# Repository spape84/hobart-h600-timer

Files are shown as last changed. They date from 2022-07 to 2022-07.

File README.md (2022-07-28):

# hobart-h600-timer
A timer pcb including 3D-printed parts and code for Hobart H600 mixing machines

## What is this about?
This repository contains everything you need to retrofit a Hobart H600 mixing machine with a timer and to build a new operating panel for the machine. I bought a Hobart H 600 (3-phase)/380V from a bakery, which went bankrupt and refurbished the machine. As the whole machine was dirty especially the operating panels I chose to replace them and add a timer function to the machine. Everything I have done is included here.

## Pictures before
tbd

## Pictures after
tbd

## Operating panel
I chose to redesign the operating panel to make it compliant to current standards. So I needed a switch to turn the machine on, another to turn it off, an emergency button, a rotary dial knob for the timer, as well as a 7-digit display.

The operating panel is only 159mm x 83mm, which is not much space for the elements planned.

You could use the file for the operating panel "Panel-0069.dxf" for laser cutting an aluminium or stainless-steel panel. I chose stainless-steel. On top of the panel I put an emergency-off button Eaton M22-PV/K11, below is a combined on/off button with control LED Eaton M22-DDL-GR-X0/X1/-A/-LED-W/-K10/-K01. The bottom row is divided into space for the 7-segment display (Adafruit 0.56" 4-Digit 7-Segment Display w/I2C Backpack) and a rotary encoder button Alps STEC12E07.

I am currently designing a backplane for the stainless-steel panel to hold the 7-segment display and the rotary encoder. So this is not ready, yet.

## Bill of materials

This is an almost complete table of everything I needed to build the new operating panel and the timer retrofit.

|Element |Producer |Product-No. |Webshop |
|---|---|---|---|
|Operating panel |self/CNC |Panel-0069.dxf |https://mipart.com/ |
|Backplane |self/3D-Print |Backplane.stl |https://mipart.com/ |
|7-segment display |Adafruit |0.56" 4-Digit 7-Segment Display |https://www.reichelt.de/ |
|Rotary Encoder |Alps |STEC12E07 |https://www.reichelt.de/ |
|PCB |self/PCB |Hobart H600 Timer.fzz |https://aisler.net/p/ZWIEMOXD|
|0603 1kohm Resistor |any |SMD-0603 1,0K |https://www.reichelt.de/ |
|0603 10kohm Resistor |any |SMD-0603 10K |https://www.reichelt.de/ |
|Transistor, SOT-23 |NXP |BC 817-40 |https://www.reichelt.de/ |
|Diode TS 4148 |any |TS 4148 |https://www.reichelt.de/ |
|Relay |Weidmueller |RCI 314012 |https://www.reichelt.de/ |
|Switching PSU |Meanwell |IRM-03-12 |https://www.reichelt.de/ |
|Arduino Nano every |Arduino |ABX00028 |https://www.reichelt.de/ |
|Terminal connector (2x) |WAGO |236-403 |https://www.reichelt.de/ |
|Terminal block |Camdenboss |CTB0502-2 |https://www.reichelt.de/ |
|Molex connector |Molex |26604040 |https://www.reichelt.de/ |
|Header w/ 2 pins 2.54 |any | |https://www.reichelt.de/ |
|Header w/ 3 pins 2.54 |any | |https://www.reichelt.de/ |
|Emergency off button |Eaton |216516 - M22-PV/K11 |https://www.automation24.de/ |
|Double pushbutton |Eaton |216700 - M22-DDL-GR-X1/X0 |https://www.automation24.de/ |
|LED element |Eaton |216557 - M22-LED-W |https://www.automation24.de/ |
|Contact element |Eaton |216378 - M22-K01 |https://www.automation24.de/ |
|Contact element |Eaton |216376 - M22-K10 |https://www.automation24.de/ |
|Mounting adapter |Eaton |216374 - M22-A |https://www.automation24.de/ |
|PCB Carrier |self/3D-Print |Timer-Mainboard-Carrier.stl |https://mipart.com/ |

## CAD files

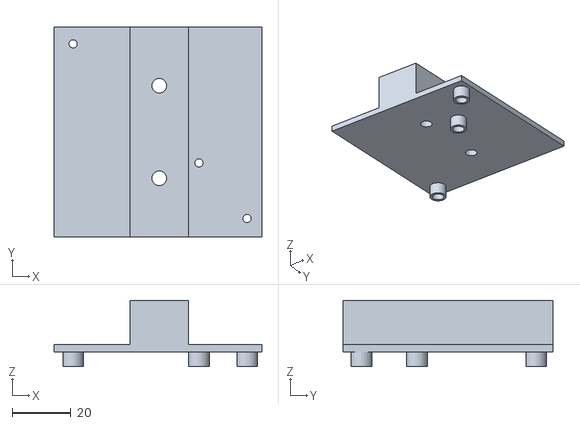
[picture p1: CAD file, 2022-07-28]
3D Print/Timer-Mainboard-Carrier.stl
70.6 x 71.4 x 22.5

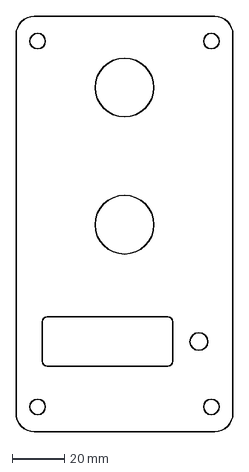
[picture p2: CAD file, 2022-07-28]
Panel/Panel-0069.dxf
83.0 x 159.0 mm

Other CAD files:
3D Print/Timer-Mainboard-Carrier_tweaked.stl
3D Print/Timer-Mainboard-Carrier.dxf
3D Print/Timer-Mainboard-Carrier.skp

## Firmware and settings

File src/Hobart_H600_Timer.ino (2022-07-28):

#include "Wire.h"
#include "EveryTimerB.h"

#ifndef _BV
#define _BV(bit) (1 << (bit)) ///< Bit-value if not defined by Arduino
#endif

//Some settings
uint8_t sw_version = 1;
uint8_t brightness = 15;
uint8_t blinkrate = 0;
long baudrate = 9600;

// This is the H600 timer state machine
unsigned int secs = 0;
bool h600running = 0;
bool timeractive = 0;

// These are old values of the state machine for debugging purposes
bool old_h600running = 0;
bool old_timeractive = 0;


// Set 0 to disable the relay for testing purposes
bool relayactive = 1;

// 7-segment display 
uint16_t volatile displaybuffer[8];
int volatile isready = 0;

// Grey Code variables
bool laston2 = 0;
bool laston3 = 0;
int state1 = 0;
int state2 = 0;

void setup() {
  pinMode(2, INPUT_PULLUP);
  pinMode(3, INPUT_PULLUP);

  pinMode(4, INPUT);
  pinMode(17, OUTPUT);

  Serial.begin(baudrate);
  Serial.print("Baudrate: ");
  Serial.println(baudrate);
  Serial.println("********************************************");
  Serial.println("Hobart H600 Timer");
  Serial.print("Version ");
  Serial.println(sw_version);
  Serial.println("2022-07-28 by Sebastian Pape");
  Serial.println("sebastian@die-knoedelwerkstatt.de");
  Serial.println("********************************************");

  startDisplay();

  TimerB2.initialize();
  TimerB2.attachInterrupt(countdown);
  TimerB2.setPeriod(1000000);

}

void countdown() {
  if (h600running == 1 && secs > 0) {
    secs--;
    printSeconds();
  }
}



void loop() {
  checkH600Running();

  // Rotary Encoder Verarbeitung
  bool curon2 = digitalRead(2);
  bool curon3 = digitalRead(3);
  if ((curon2 != laston2) != (curon3 != laston3)) {
    laston2 = curon2;
    laston3 = curon3;
    int curstate = curon3 + 2 * curon2;
    if (curstate == 3 && state1 == 2 && state2 == 0) {
      goRight();
    }
    if (curstate == 3 && state1 == 1 && state2 == 0 && secs > 0) {
      goLeft();
    }
    state2 = state1;
    state1 = curstate;
  }

  if (isready == 1) {
    writeToDisplay();
    Serial.println("Display: WRITE");
  }

  if(old_timeractive != timeractive) {
    Serial.print("Timeractive: ");
    Serial.println(timeractive);
    old_timeractive = timeractive;
  }

  if(old_h600running != h600running) {
    Serial.print("H600Running: ");
    Serial.println(h600running);
    old_h600running = h600running;
  }
}

void goLeft() {
  if (secs <= 15) {
    secs = 0;
    printHold();
    timeractive = 0;
  } else {
    secs = secs - 15;
    printSeconds();
    Serial.println("Encoder: LEFT");
    Serial.print("Seconds: ");
    Serial.println(secs);
  }
}

void goRight() {
  timeractive = 1;
  secs = secs + 15;
  if(secs >= 3600) {
    secs = 0;
    printHold();
    timeractive = 0;
  } else {
    printSeconds();
    Serial.println("Encoder: RIGHT");
    Serial.print("Seconds: ");
    Serial.println(secs);
  }
}

void checkH600Running() {
  if (digitalRead(4) == HIGH) {
    h600running = 1;
    if (timeractive == 1 && secs == 0) {
      printSeconds();
      writeToDisplay();
      stoph600();
      Serial.println("Timer: END");
    }
  } else {
    h600running = 0;
  }
}

/*
 * Stop the H600 by pulling the relay and releasing it a second later
 * This makes the contactor stop the motor.
 */
 
void stoph600() {
  timeractive = 0;
  Serial.println("Relay: PULL");
  if (relayactive) digitalWrite(17, HIGH);
  delay(1000);
  Serial.println("Relay: RELEASE");
  if (relayactive) digitalWrite(17, LOW);
  printHold();
}


/*
 * 7-segment display methods
 * 
 *
*/

/*
 * Prepare the display, clear the memory and print the word "HOLd" to the display
 */
 
void startDisplay(void) {
  Wire.begin();
  Wire.beginTransmission(0x70);
  Wire.write(0x21);
  Serial.println("Sending 0x21, with length 1");
  int returncode = Wire.endTransmission();
  Serial.print("Return Code: ");
  Serial.println(returncode);

  setBrightness();
  setBlinkRate();
  
  clearDisplayBuffer();

  writeToDisplay();

  printH600();

  writeToDisplay();

  delay(1000);

  printHold();

  writeToDisplay();
}

/* 
 *  convert the displaybuffer[8] to a buffer
 *  for the i2c 7-segment display
 */
 
void writeToDisplay(void) {
  uint8_t buffer[17];

  buffer[0] = 0x00;

  for (uint8_t i = 0; i < 8; i++) {
    buffer[1 + 2 * i] = displaybuffer[i] & 0xFF;
    buffer[2 + 2 * i] = displaybuffer[i] >> 8;
  }

  Wire.beginTransmission(0x70);
  Wire.write(buffer, 17);
  int returncode = Wire.endTransmission();
  isready = 0;
  if (returncode != 0) {
    Serial.print("i2c Error Display: ");
    Serial.println(returncode);
  }
}

void clearDisplayBuffer() {
  for (uint8_t i = 0; i < 8; i++) {
    displaybuffer[i] = 0;
  }
}

/* 
 *  Print the word "HOLd" to the 7-digit display.
 */

void printHold() {
  clearDisplayBuffer();
  displaybuffer[0] = 0b01110110;
  displaybuffer[1] = 0b00111111;
  displaybuffer[3] = 0b00111000;
  displaybuffer[4] = 0b01011110;
  Serial.println("Display: HOLD");
  isready = 1;
}

void printH600() {
  displaybuffer[0] = 0b01110110;
  displaybuffer[1] = 0b01111101;
  displaybuffer[3] = 0b00111111;
  displaybuffer[4] = 0b00111111;
  Serial.println("Display: H600");
  isready = 1;
}


/* 
 *  Prepare the number of seconds for the display and convert it to
 *  an integer representing minutes and seconds
 */
 
void printSeconds() {
  printNumber(((secs / 60) * 100) + (secs % 60));
}


/*
 * Print any integer/number between 0 and 9999.
 * Display a colon between 100th and 10th (displaybuffer[2])
 * 
 * int number: the number to display
 */
 
void printNumber(int number) {
  if (number > 9999 || number < 0) {
    return;
  }
  clearDisplayBuffer();
  displaybuffer[0] = getDigit(number / 1000);
  displaybuffer[1] = getDigit((number % 1000) / 100);
  displaybuffer[2] = 0b00111111;
  displaybuffer[3] = getDigit((number % 100) / 10);
  displaybuffer[4] = getDigit((number % 10));
  isready = 1;
}

/*
 * Return the binary code for digits 0 - 9
 * 
 * int val: the digit to return the binary code for
 */
int getDigit(int val) {
  uint8_t digittable[] = {
    0b00111111,
    0b00000110,
    0b01011011,
    0b01001111,
    0b01100110,
    0b01101101,
    0b01111101,
    0b00000111,
    0b01111111,
    0b01101111
  };
  return digittable[val];
}

void setBrightness() {
  uint8_t buffer = 0xE0 | brightness;
  Wire.beginTransmission(0x70);
  Wire.write(buffer);
  Serial.print("Sending ");
  Serial.print(buffer);
  Serial.println(", with length 1");
  int returncode = Wire.endTransmission();
  Serial.print("Return Code: ");
  Serial.println(returncode);
}

void setBlinkRate() {
  uint8_t buffer = 0x80 | 0x01 | (blinkrate << 1);
  Wire.beginTransmission(0x70);
  Wire.write(buffer);
  Serial.print("Sending ");
  Serial.print(buffer);
  Serial.println(", with length 1");
  int returncode = Wire.endTransmission();
  Serial.print("Return Code: ");
  Serial.println(returncode);
}

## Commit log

2022-07-28 Code for the project
    Arduino Nano Every based
2022-07-28 Added all hardware stuff
    [Hobart H600 Timer.fzz, Panel-0069.dxf, Timer-Mainboard-Carrier.dxf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]
